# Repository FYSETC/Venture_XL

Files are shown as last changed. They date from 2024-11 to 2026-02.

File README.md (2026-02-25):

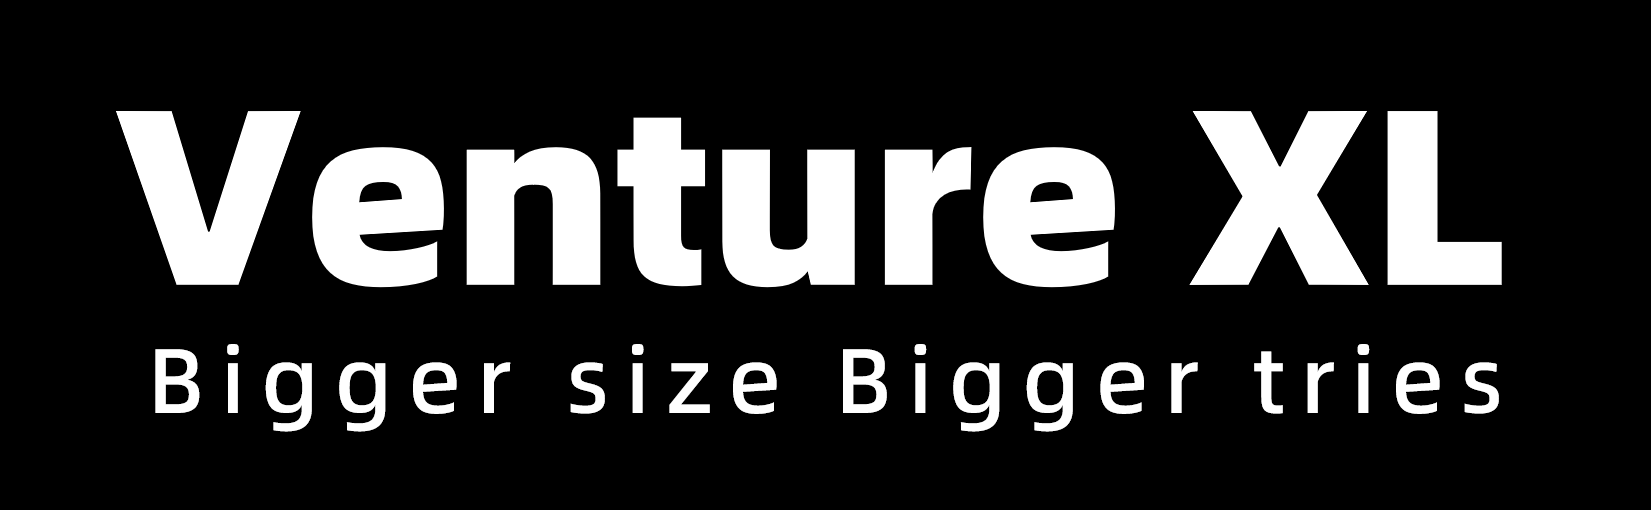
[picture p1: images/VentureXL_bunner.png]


# Introduction

The Venture XL, a 600mm3 coreXY printer kit, is inspired by the classic VORON V2.4. The key components of this kit are high-precision CNC-machined parts, demonstrating outstanding quality. Meanwhile, it comes with the necessary printing components and tools considerately, and the print head and control box have been pre - assembled, enabling you to start the installation process effortlessly without the need to prepare additional parts. Once the installation is completed, you can immediately engage in the printing work and enjoy an efficient and convenient printing experience.

It is equipped with a 550Mhz H723 single - chip microcomputer, an RK3568 with 4 cores at 2.0GHz, 2GB + 32GB for the host computer, a TMC5160 high - performance stepper motor driver, and a 7 - inch high - definition capacitive touch screen. With a printing speed of up to 500m/s and an acceleration of 50000, it not only brings an extremely fast printing experience but also creates a comfortable operation feeling for you.

The size of the machine frame is designed with reserved installation spaces for IDEX and AWD, providing you with broad possibilities for upgrade and modification, which is highly playable. Whether you are pursuing higher performance or personalized customization, you can find satisfaction here.

In addition, the complete enclosure design provides an insulated space for the printer, effectively maintaining the stability of the printing environment. At the same time, it also has powerful air - purification capabilities. It can support the printing of various consumables and, more importantly, minimize the potential threat of plastic particles to your health to the greatest extent, creating a safe and comfortable printing environment for you.

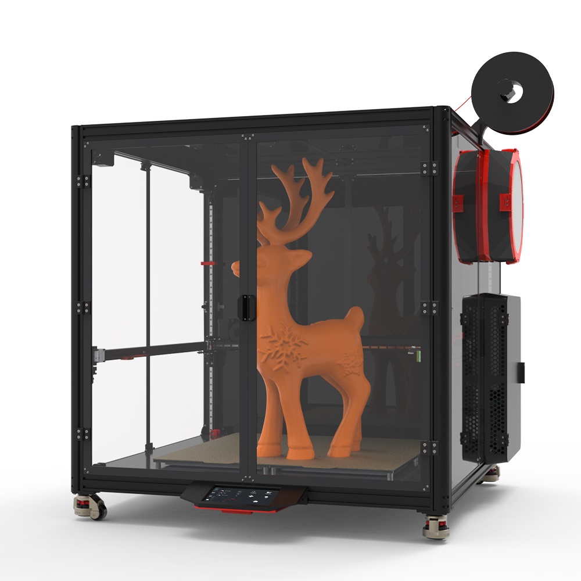
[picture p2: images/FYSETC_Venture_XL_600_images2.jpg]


# Features

## Electronics：

- RK3568 (2+32GB) 4 core A55 2.0GHz Host
- Spider Pro 2.0 Controller, 550Hz H723
- SB Combo V2 control board (Via CANBUS)
- 7-inch FHD optically bonded capacitive touch screen
- RGB lighting system , Horizontal RGB lighting (84 LEDs) & SB LOGO RGB (10 LEDs) & Vertical RGB lighting (2x84 LEDs)
- Dual 350W PSU, 48V+24V
- BIG5160+TMC2209 stepper motor driver
- High-power 63A/40A contactor
- Four-zone independent control hot bed
- Pre-assembled independent control box
- 4xZ reduction motor
- 2.5A high temperature, high torque XY motor
- Cartographer 3D Eddy Current Sensor
- Filament sensor
- Logitech C270 Camera 

## Mechanical

- Super large size: 910x910x940mm, can meet AWD or IDEX upgrade modification;

- Enclosed cavity, more materials can be printed, healthier printing method, the box is sealed by segmented assembly, easy to install and ensure structural strength;

- Compatible with Nevermore StealthMax air filter, the air quality in the box is guaranteed to be pollution-free when the box is sealed;

- 4040 aluminum profile frame, light and high strength;

- CNC precision-machined independent four-zone printing platform, can be fine-tuned according to flatness;

- Drag chain system;

- 12mm linear guide, 9mm super wear-resistant belt;

- Aluminum alloy external electric control box that can be placed arbitrarily (left/right/back), connect the line;

- CNC aluminum alloy link components to ensure the structural strength of the equipment;

- Z-axis 27:1 reduction motor ensures that the Z-axis is more stable and does not slip when the machine is running or stopped;

- IDMCNC metal bracket can withstand high temperature challenges and ensure stability. In a high-temperature printing environment, it will not deform or fail, ensuring long-lasting and reliable performance. The bracket weighs only 26g, which is lighter than TAP leveling and old-style proximity switches. The bracket weighs only 26g, which is lighter than TAP leveling and old-style proximity switches, reducing inertia and improving speed, accuracy and printing quality;

- Can hang 5KG large rolls of consumables, and there is no need to frequently replace consumables during printing;

- 40KG load Foma wheel allows the equipment to be stationed and transported at any time

# Bill of Materials

| Index | Sort | Component | Qty |
| ----- | --- | --- | --- |
| 1 | Fasteners | Venture XL Fasteners Pack | 1 SET  |
| 2 | Motion | GATES GT2 Open Belt LL-2GT-9 (9mm wide) - 3400mm | 2 PCS  |
| 3 | Motion | GATES GT2 Open Belt LL-2GT-9 (9mm wide) - 1800mm | 4 PCS  |
| 4 | Motion | GT2 20T Toothed Idler (8mm ID 9mm W) | 4 PCS  |
| 5 | Motion | GT2 20T Toothed Idler (5mm ID 9mm W) | 2 PCS  |
| 6 | Motion | F695-2RS Bearing | 48 PCS |
| 7 | Motion | 695-ZZ Bearing | 24 PCS |
| 8 | Motion | 5x29mm Shaft | 4 PCS  |
| 9 | Motion | MGN9H Linear Rail and Carriage 720mm | 4 PCS  |
| 10 | Motion | MGN9H Linear Rail and Carriage 760mm | 2 PCS  |
| 11 | Motion | MGN12H Linear Rail and Carriage 760mm | 1 PCS  |
| 12 | Vibration Management | Universal Fomar Caster | 4 PCS  |
| 13 | Electronics | Stealthburner CAN Toolhead Board | 1 SET  |
| 14 | Electronics | X AXIS ENDSTOP OMRON MICROSWITCH | 1 SET  |
| 15 | Electronics | Y AXIS ENDSTOP OMRON MICROSWITCH | 1 SET  |
| 16 | Electronics | Cartographer 3D Eddy Current Sensor | 1 SET  |
| 17 | Electronics | NeoPixel RGBW Mini Button PCB LED | 1 SET  |
| 18 | Electronics | Four-way solid state relay | 1 PCS  |
| 19 | Electronics | AC contactor | 1 PCS  |
| 20 | Electronics | Rocker Switch | 1 PCS  |
| 21 | Electronics | AC pin socket | 1 PCS  |
| 22 | Electronics | 42HSC8418-19PG27S(check [here](https://github.com/FYSETC/FYSETC-MOTORS/tree/main/42HSC8418-19PG27S)) | 4 PCS  |
| 23 | Electronics | 42HSC8418-37(check [here](https://github.com/FYSETC/FYSETC-MOTORS/tree/main/42HSC8418-37))  | 2 PCS  |
| 24 | Electronics | 40x40x10 Axial Fan (24V)  Dual Ball Bearing with heat sink | 2 PCS  |
| 25 | Electronics | G36HSY4405-6D-60(check [here](https://github.com/FYSETC/FYSETC-VORON-2.4-R2-Pro/tree/main/Docs/Stepper%20motor%20parameters)) | 1 PCS  |
| 26 | Electronics | Meanwell 350W-24V Power supply | 1 PCS  |
| 27 | Electronics | Meanwell350W-48V Power supply | 1 PCS  |
| 28 | Electronics | 30x30x7 Axial Fan (24V) | 1 PCS  |
| 29 | Electronics | 40x40x10 Axial Fan (24V)  Dual Ball Bearing | 1 PCS  |
| 30 | Electronics | 50x50x15 Centrifugal Fan (24V)  Dual Ball Bearing | 1 PCS  |
| 31 | Electronics | 90x90x15 Axial Fan (24V)  Dual Ball Bearing | 1 PCS  |
| 32 | Electronics | Keystone CAT6 Insert | 1 PCS  |
| 33 | Electronics | Terminal block (one in, four out) | 1 PCS  |
| 34 | Electronics | C13 Power Cord / NEMA5-20-C19 | 1 PCS  |
| 35 | Electronics | Gantry light bar power board | 1 PCS  |
| 36 | Electronics | Gantry light bar | 1 PCS  |
| 37 | Electronics | Lighting strips | 1 PCS  |
| 38 | Electronics | C270 Camera | 1 PCS  |
| 39 | Electronics | Electronic box (assembled ) | 1 PCS  |
| 40 | Controller | ~~sdcard 16GB~~ | 1 PCS  |
| 41 | Controller | USB2.0 A-C cable &  USB3.0 A-A cable | 1 PCS  |
| 42 | Controller | Spider_Pro_V1.0 | 1 PCS  |
| 43 | Controller | TMC2209 Stepper Motor Driver | 4 PCS  |
| 44 | Controller | BIG 5160 Stepper Motor Driver | 2 PCS  |
| 45 | Controller | 7-inch screen controller assembly set | 1 SET  |
| 46 | Frame | OpenBuilds | 12 PCS |
| 47 | Frame | Misumi sectional profile Kit（23 Pcs） | 1 SET  |
| 48 | Frame | Sealing profile kit（12 Pcs） | 1 SET  |
| 49 | Misc | PTFE Tube (4mm OD 2mm ID) - 3m | 1 PCS  |
| 50 | Misc | 6x3mm Neodimium Magnet | 12 PCS |
| 51 | Misc | Stealthburner kits | 1 SET  |
| 52 | Misc | PH2.0 2/3/4 Pin Plastic shell | 1 SET  |
| 53 | Misc | XH2.54 2/3/4 Pin Plastic shell | 1 SET  |
| 54 | Mics | Zip ties | 1 SET  |
| 55 | Mics | Saddle type cable tie holder | 1 SET  |
| 56 | Cables | Cable Kit（Pre-crimped terminals and longer wire lengths with label） | 1 SET  |
| 57 | Cables | VORON Chain Kit (10X10mm) | 3 PCS  |
| 58 | Panels | Bottom / Back / Side / Front / Top / Electric box Panels | 13 PCS |
| 59 | Buildplate | 6061 Plate - 302X302x5mm （Surface milling improve flatness） | 4 PCS  |
| 60 | Buildplate | Silicone AC Heater - 250x250mm (450W)+Thermal Fuse RH15A125（Pluggable） | 4 PCS  |
| 61 | Buildplate | JanusBPS Textured steel plate 605 x 605mm （Double-sided powder gold） | 1 PCS  |
| 62 | Buildplate | Scratch-proof Magnetic stickers 300X300mm thickness 1.5mm | 1 PCS  |
| 63 | Buildplate | Hotbed Insulation cotton thickness 5mm | 1 PCS  |
| 64 | Buildplate | VORON hot bed PEI limit baffle | 1 PCS  |
| 65 | Buildplate | VORON Hotbed nylon column | 1 SET  |
| 66 | Buildplate | Hot bed leveling spring | 1 SET  |
| 67 | Buildplate | VORON IDM Scanner CNC 9mm belt | 1 SET  |
| 68 | Tool | Electric soldering iron（With 500mm tin wire） | 1 PCS  |
| 69 | Tool | Heat-inserted nut kit | 1 SET  |
| 70 | Tool | Cutting pliers | 1 PCS  |
| 71 | Tool | Tweezers | 1 PCS  |
| 72 | Tool | Screwdriver (Phillips/Slotted) | 1 SET  |
| 73 | Tool | Hexagonal wrenchs | 1 SET  |
| 74 | Tool | Thermal silica | 1 PCS  |
| 75 | Tool | Key Puller | 1 PCS  |
| 76 | Misc | 3M VHB Tape 5952 | 1 PCS  |
| 77 | Tool | Shielding tape | 1 PCS  |
| 78 | Tool | Acetate cloth tape | 1 PCS  |
| 79 | Tool | Steel brush | 1 PCS  |
| 80 | Mics | Nevermore StealthMax | 1 SET  |
| 81 | Mics | Hinge | 8 PCS  |
| 82 | Mics | Braided Sleeve | 1 SET  |
| 83 | Mics | Aluminum profile flat sealing strip | 1 SET  |
| 84 | Mics | The standby line 3m | 1 PCS  |

# To Do Task

As an open source machine, it has unlimited possibilities. We will do our best to improve its information and tutorials. At the same time, we also invite professional players to contribute their ideas and strength. Below is part of our task progress, welcome to claim it.

|  TASK  | STATUS |  Author |
| ---- | ---- | ---- |
| Instruction manual: Paper wiring diagram included with the kit | [x] | FYSETC |
| Instruction manual: Quick guide to simple configuration included with the kit | [x] | FYSETC |
| Tutorial: Wiring tutorial | (i) | FYSETC |
| Tutorial: Structural installation video | [i] | FYSETC |
| Tutorial: Configuration tutorial | [x] | FYSETC |
| Tutorial: Common problems and solutions | (i) | FYSETC |
| Tutorial: Common slicing software configuration, Prusa Slicer / Bambu Slicer / Orca Slicer | [x] | FYSETC |
| Tutorial: Combo V2 USB usage guide | |  |
| Tutorial: AWD modification guide | | |
| Tutorial: IDEX modification tutorial | | |
| Tutorial: A more perfect wiring tutorial | (i) | Esoterical |
| Tutorial: Structural installation video | | |
| Tutorial: Wiring tutorial | | |
| Tutorial: Configuration tutorial | | |
| Evaluation: Speed limit | | |
| Evaluation: Common problems and solutions | | |

# Known issue

1.  Instructions for use of motor connection wire:
    Z0 and Z3 motors need to use 3.5m connecting wires, Z1 motor uses 1.85m connecting wires, and the connecting wires of Z2 motor and B motor are swapped to solve the problem of short connecting wire of B motor. A Motor connection line remains unchanged
    
2. Update Notes

| Column |images |Installation location |Download Link | |
| - | - | - | - | - |
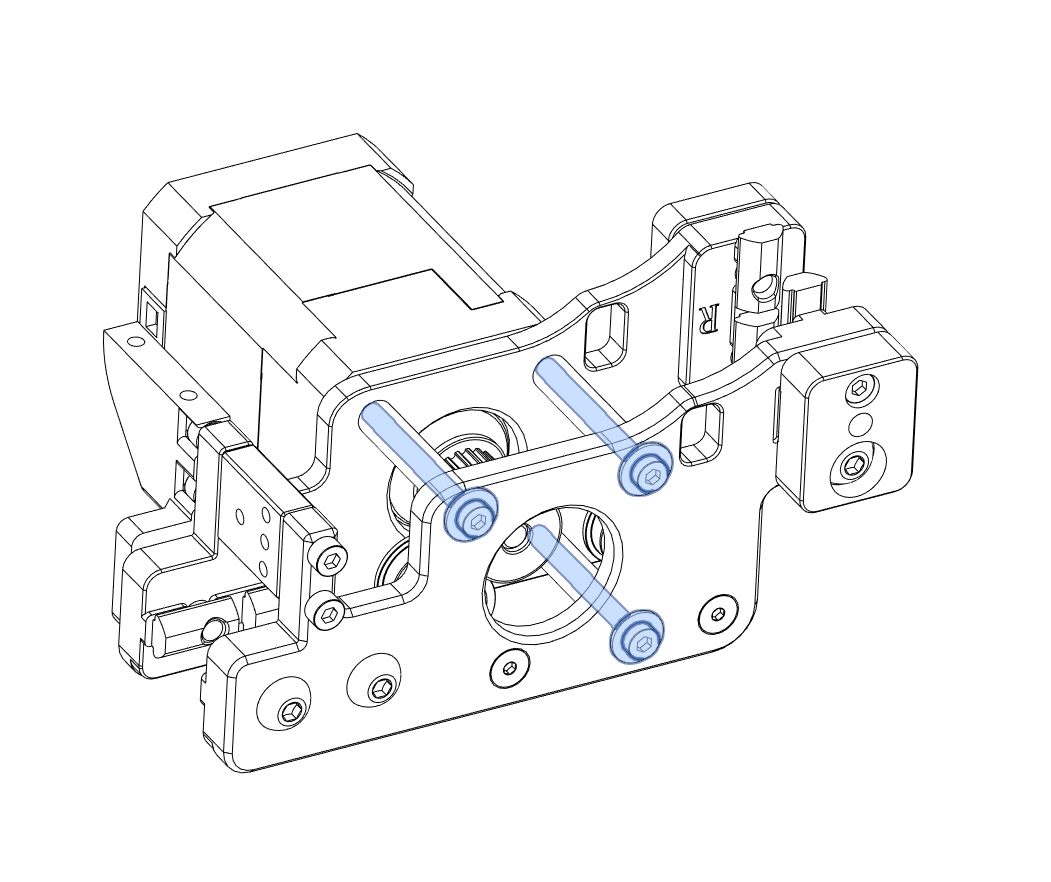
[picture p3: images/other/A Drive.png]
A Drive.png
|1 | |Manual page 26 | |The M3x40 motor mounting screws are a bit long, so you can use M3x38 instead, or add M3 washers and use M3x40 for installation. |
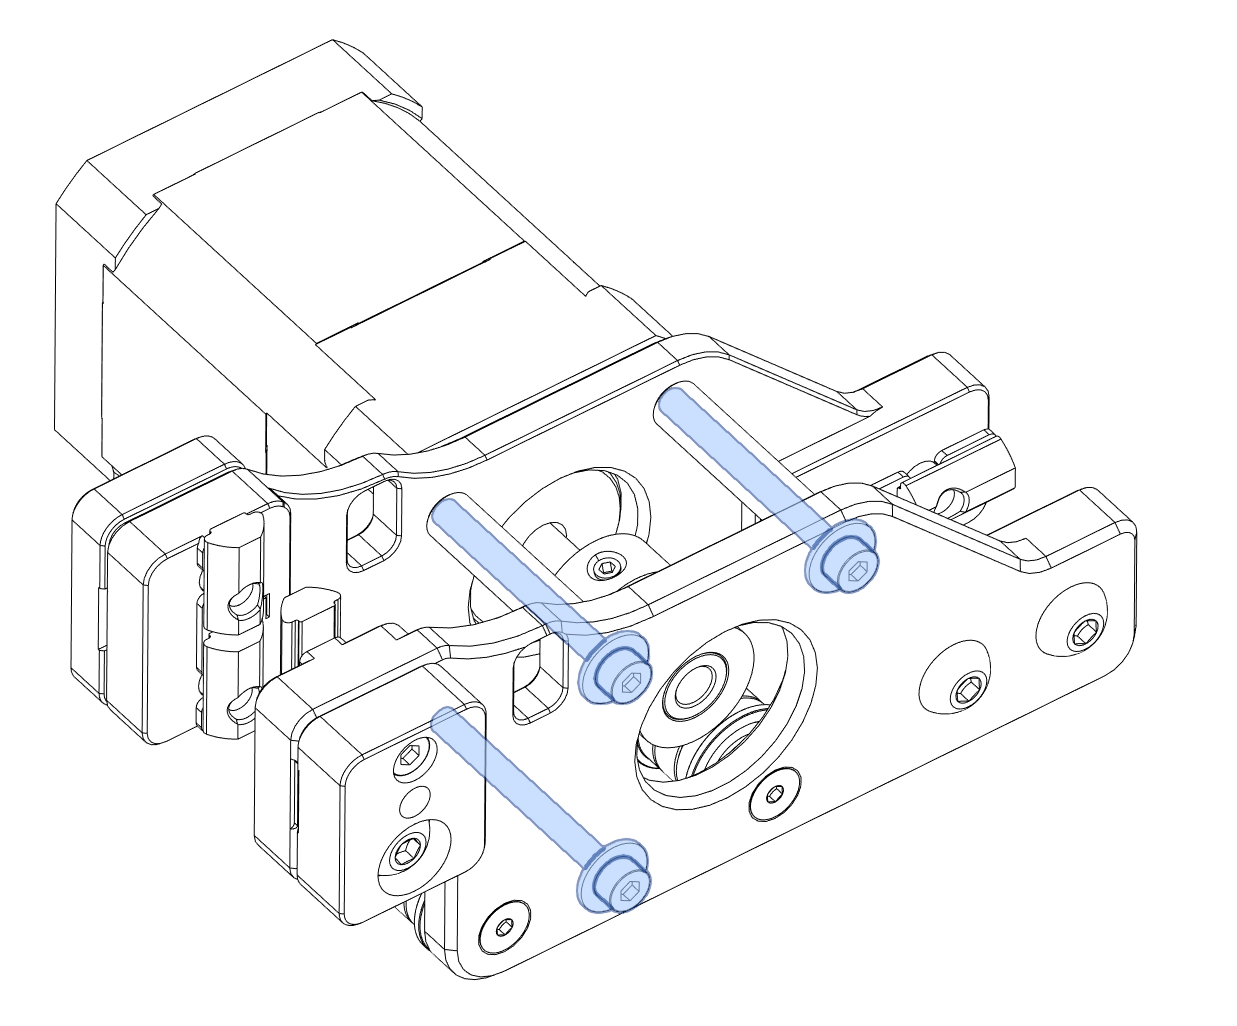
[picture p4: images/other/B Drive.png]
B Drive.png
|2 | |Manual page 27 | |The M3x40 motor mounting screws are a bit long, so you can use M3x38 instead, or add M3 washers and use M3x40 for installation.  |
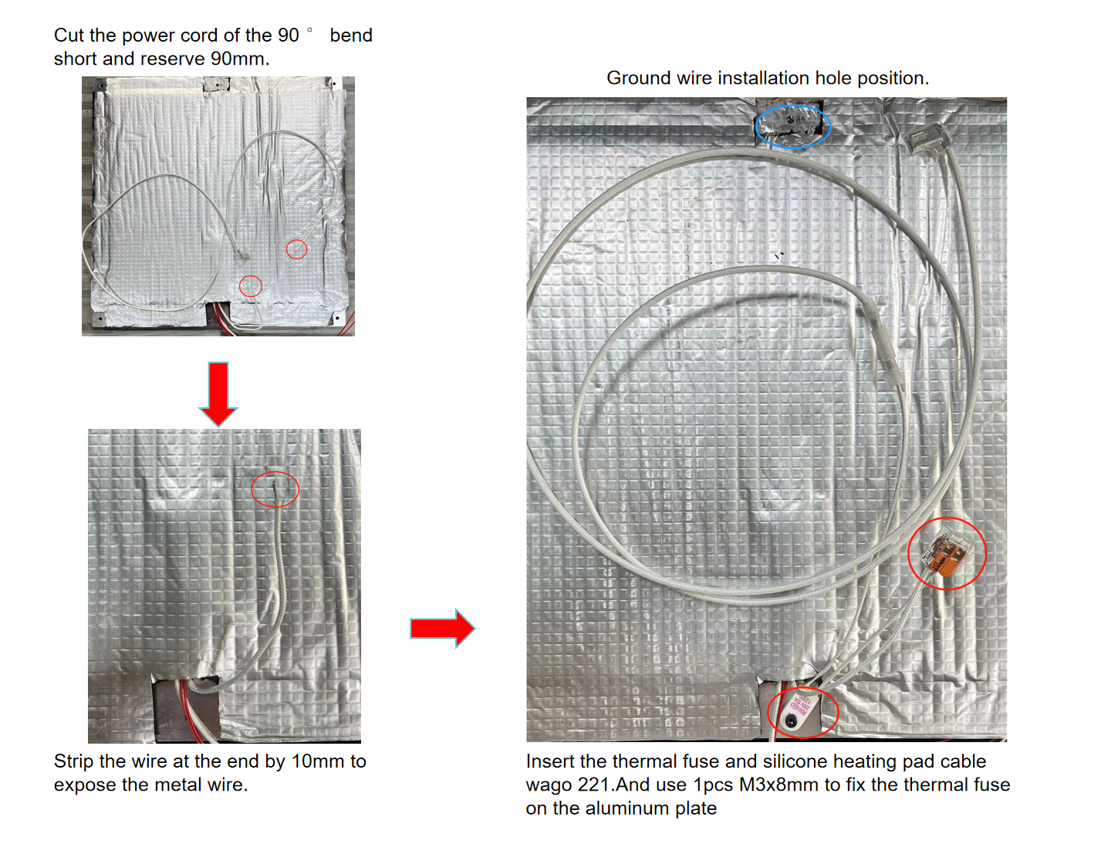
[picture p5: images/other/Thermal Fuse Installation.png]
Thermal Fuse Installation.png
|3 | |Manual page 43 | |Added 4 pcs hot bed thermal fuse |
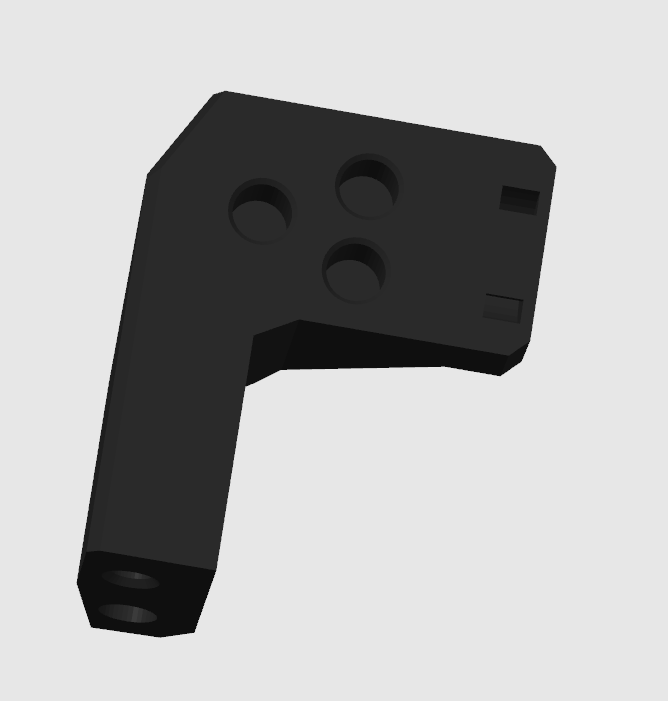
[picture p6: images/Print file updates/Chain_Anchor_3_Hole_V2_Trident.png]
|4 | |Manual page 48 |[here](https://github.com/FYSETC/Venture_XL/blob/main/STLs/Need%20to%20print%20the%20document%20yourself/Stealthburner/Chain_Anchor_3_Hole_V2_Trident.STL) | |
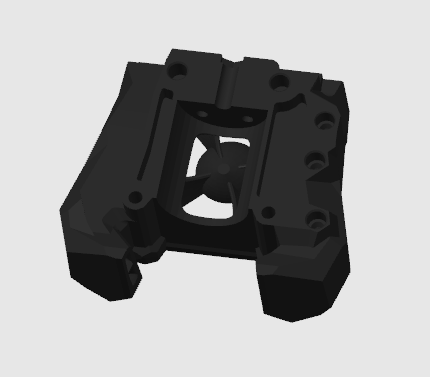
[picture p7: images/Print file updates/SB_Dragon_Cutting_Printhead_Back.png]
|5 | |Manual page 48 |[here](https://github.com/FYSETC/Venture_XL/blob/main/STLs/Need%20to%20print%20the%20document%20yourself/Stealthburner/SB_Dragon_Cutting_Printhead_Back.STL) | |
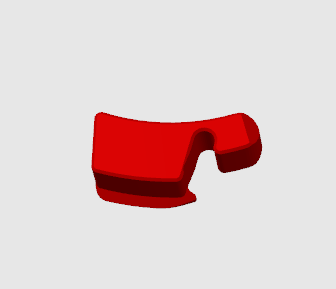
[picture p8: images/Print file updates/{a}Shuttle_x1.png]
|6 | |Manual page 49 |[here](https://github.com/FYSETC/Venture_XL/blob/main/STLs/Need%20to%20print%20the%20document%20yourself/Stealthburner/%7Ba%7DShuttle_x1.STL) | |
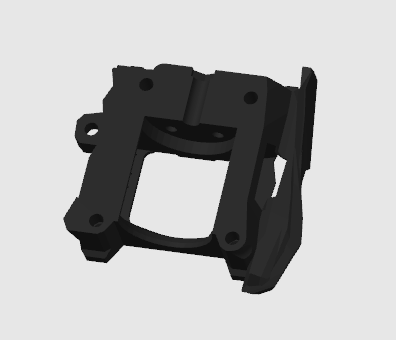
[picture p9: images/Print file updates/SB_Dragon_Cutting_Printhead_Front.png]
|7 | |Manual page 50 |[here](https://github.com/FYSETC/Venture_XL/blob/main/STLs/Need%20to%20print%20the%20document%20yourself/Stealthburner/SB_Dragon_Cutting_Printhead_Front.STL) | |
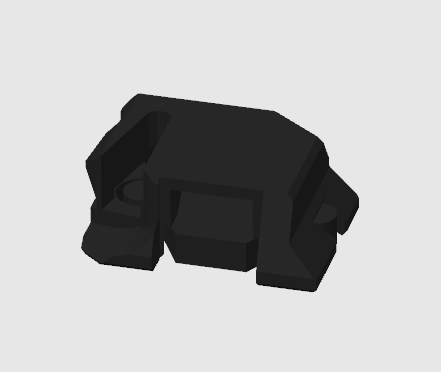
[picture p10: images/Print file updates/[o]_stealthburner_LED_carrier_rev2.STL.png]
|8 | |Manual page 52 |[here](https://github.com/FYSETC/Venture_XL/blob/main/STLs/Need%20to%20print%20the%20document%20yourself/Stealthburner/%5Bo%5D_stealthburner_LED_carrier_rev2.STL.stl) | |
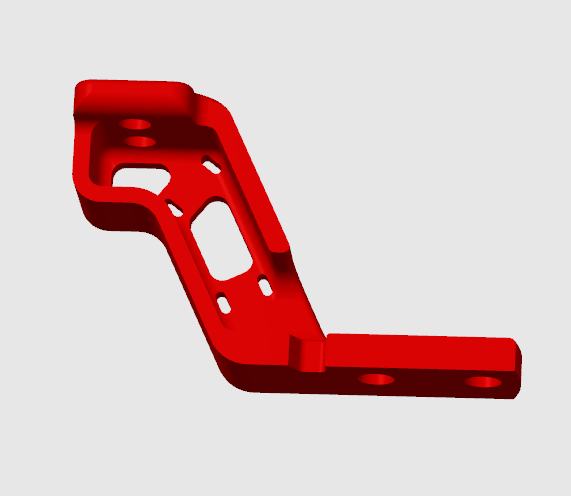
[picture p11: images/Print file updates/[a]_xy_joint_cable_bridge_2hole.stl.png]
|9 | |Manual page 53 |[here](https://github.com/FYSETC/Venture_XL/blob/main/STLs/Need%20to%20print%20the%20document%20yourself/XY_Joints/%5Ba%5D_xy_joint_cable_bridge_2hole.stl.stl) | |
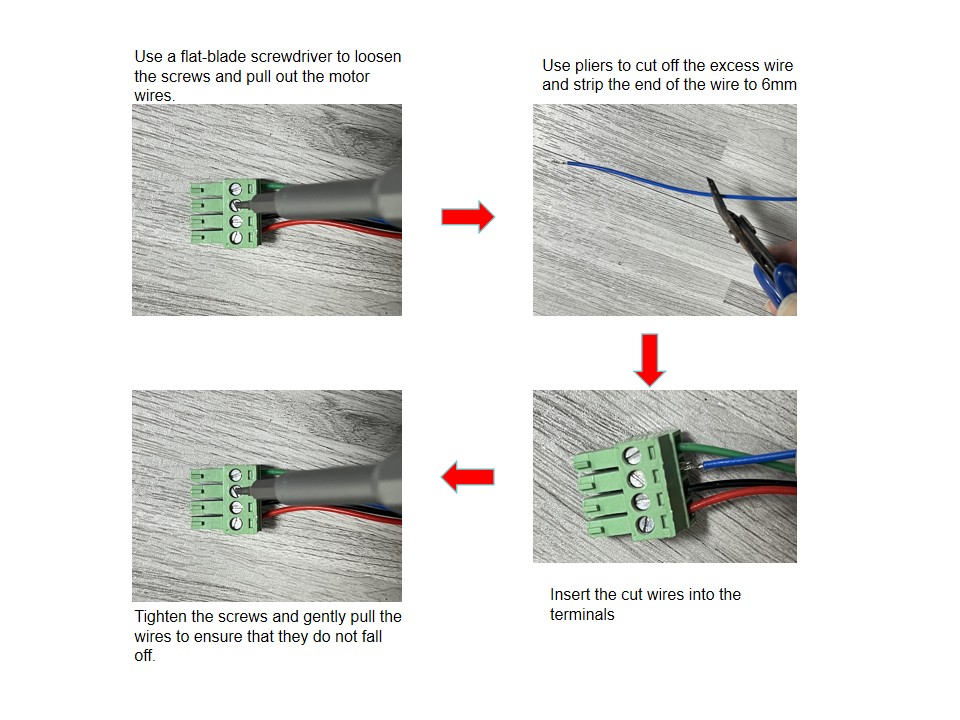
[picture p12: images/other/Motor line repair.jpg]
Motor line repair.jpg
|10 | | | |Motor line repair |
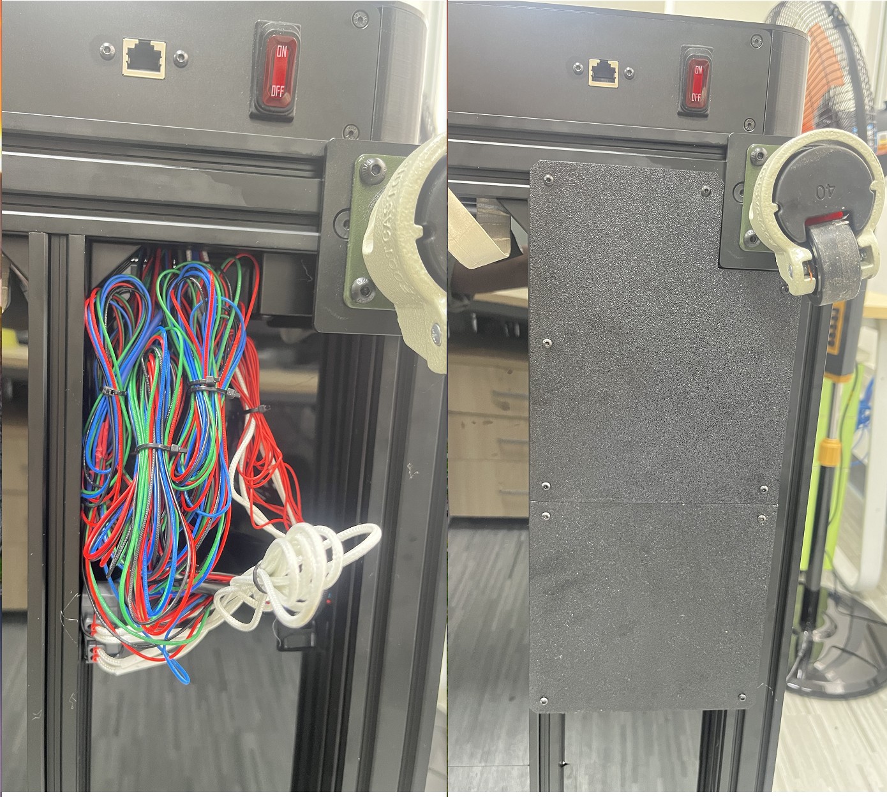
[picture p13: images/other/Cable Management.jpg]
Cable Management.jpg
|11 | |Manual page 59 |[here](https://github.com/FYSETC/Venture_XL/blob/main/STLs/Need%20to%20print%20the%20document%20yourself/Under%20Floor%20Wire%20Cover/Under%20Floor%20Wire%20Cover_1_x1.STL)  [here](https://github.com/FYSETC/Venture_XL/blob/main/STLs/Need%20to%20print%20the%20document%20yourself/Under%20Floor%20Wire%20Cover/Under%20Floor%20Wire%20Cover_2_x1.STL) |Add bottom cable cover |

**Please provide the order number to contact customer service to collect the supplementary accessory package.**

3. Notice

Venture_XL CAD need to use WinRAR to decompress, otherwise the file cannot be opened.

4.Instructions

We have updated the installation guide on WIKI,；
link:(https://wiki.fysetc.com/docs/Venture_XL)

5.Version 2 - Spider King

The motherboard has been updated and replaced with Spider King.
Replaced mainboard, updated wiring diagram

# Thanks to
Here I would like to express my gratitude and support to Esoterical、 RichardTHF and many others. Your suggestions have helped us a lot - you all have my most sincere thanks.

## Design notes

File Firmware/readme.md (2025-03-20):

RK3568 img: Mega 

https://mega.nz/fm/XEJgVJ6b

Cartographer:

https://docs.cartographer3d.com/cartographer-probe/installation-and-setup

Spider Pro:

https://github.com/FYSETC/Spider_Pro

SB Combo:

https://wiki.fysetc.com/SB_Combo_V2/

https://github.com/FYSETC/SB_Combo_V2

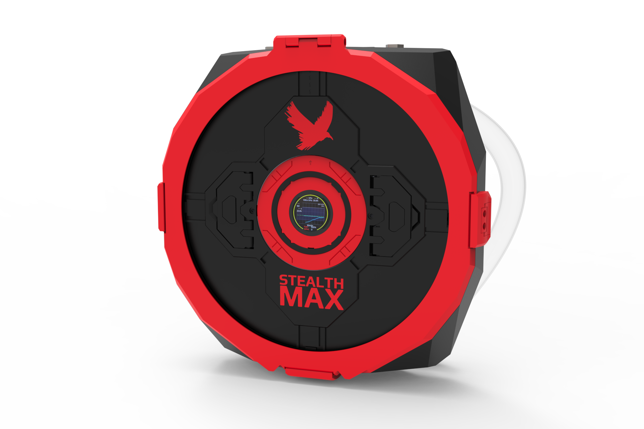
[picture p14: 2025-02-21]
images/Venture_XL_600_StealthMax.png

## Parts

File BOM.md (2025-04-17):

# Package list 

## Venture_XL V1.0

| Index | Sort | Component | Qty | Note |
| ----- | --- | --- | --- | --- |
| 1 | Fasteners | Venture XL Fasteners Pack | 1 SET  | |
| 2 | Motion | GATES GT2 Open Belt LL-2GT-9 (9mm wide) - 3400mm | 2 PCS  | |
| 3 | Motion | GATES GT2 Open Belt LL-2GT-9 (9mm wide) - 1800mm | 4 PCS  | |
| 4 | Motion | GT2 20T Toothed Idler (8mm ID 9mm W) | 4 PCS  | |
| 5 | Motion | GT2 20T Toothed Idler (5mm ID 9mm W) | 2 PCS  | |
| 6 | Motion | F695-2RS Bearing | 48 PCS | |
| 7 | Motion | 695-ZZ Bearing | 24 PCS | |
| 8 | Motion | 5x29mm Shaft | 4 PCS  | |
| 9 | Motion | MGN9H Linear Rail and Carriage 720mm | 4 PCS  | |
| 10 | Motion | MGN9H Linear Rail and Carriage 760mm | 2 PCS  | |
| 11 | Motion | MGN12H Linear Rail and Carriage 760mm | 1 PCS  | |
| 12 | Vibration Management | Universal Fomar Caster | 4 PCS  | |
| 13 | Electronics | Stealthburner CAN Toolhead Board | 1 SET  | |
| 14 | Electronics | X AXIS ENDSTOP OMRON MICROSWITCH | 1 SET  | |
| 15 | Electronics | Y AXIS ENDSTOP OMRON MICROSWITCH | 1 SET  | |
| 16 | Electronics | ADXL__Hybrid_IDM | 1 SET  | |
| 17 | Electronics | NeoPixel RGBW Mini Button PCB LED | 1 SET  | |
| 18 | Electronics | Four-way solid state relay | 1 PCS  | |
| 19 | Electronics | AC contactor | 1 PCS  | |
| 20 | Electronics | Rocker Switch | 1 PCS  | |
| 21 | Electronics | AC pin socket | 1 PCS  | |
| 22 | Electronics | 42HSC8418-19PG27S | 4 PCS  | |
| 23 | Electronics | 42HSC8418-37 | 2 PCS  | |
| 24 | Electronics | 40x40x10 Axial Fan (24V)  Dual Ball Bearing with heat sink | 2 PCS  | |
| 25 | Electronics | G36HSY4405-6D-60(check [here](https://github.com/FYSETC/FYSETC-VORON-2.4-R2-Pro/tree/main/Docs/Stepper%20motor%20parameters)) | 1 PCS  | |
| 26 | Electronics | 350W-24V Power supply | 1 PCS  | |
| 27 | Electronics | 350W-48V Power supply | 1 PCS  | |
| 28 | Electronics | 30x30x7 Axial Fan (24V) | 1 PCS  | |
| 29 | Electronics | 40x40x10 Axial Fan (24V)  Dual Ball Bearing | 1 PCS  | |
| 30 | Electronics | 50x50x15 Centrifugal Fan (24V)  Dual Ball Bearing | 1 PCS  | |
| 31 | Electronics | 90x90x15 Axial Fan (24V)  Dual Ball Bearing | 1 PCS  | |
| 32 | Electronics | Keystone CAT6 Insert | 1 PCS  | |
| 33 | Electronics | Terminal block (one in, four out) | 1 PCS  | |
| 34 | Electronics | C13 Power Cord / NEMA5-20-C19 | 1 PCS  | |
| 35 | Electronics | Gantry light bar power board | 1 PCS  | |
| 36 | Electronics | Gantry light bar | 1 PCS  | |
| 37 | Electronics | Lighting strips | 1 PCS  | |
| 38 | Electronics | Camera | 1 PCS  | |
| 39 | Electronics | Electric box | 1 PCS  | |
| 40 | Controller | sdcard 16GB | 1 PCS  | |
| 41 | Controller | USB C cable | 1 PCS  | |
| 42 | Controller | Spider_Pro_V1.0 | 1 PCS  | |
| 43 | Controller | TMC2209 Stepper Motor Driver | 4 PCS  | |
| 44 | Controller | BIG 5160 Stepper Motor Driver | 2 PCS  | |
| 45 | Controller | 7-inch screen controller assembly (7-inch display + CM68 control board + display cable + CM68 radiator + 4010 cooling fan + printed housing) | 1 SET  | |
| 46 | Frame | OpenBuilds | 12 PCS | |
| 47 | Frame | Misumi sectional profile Kit（23 Pcs） | 1 SET  | |
| 48 | Frame | Sealing profile kit（12 Pcs） | 1 SET  | |
| 49 | Misc | PTFE Tube (4mm OD 2mm ID) - 3m | 1 PCS  | |
| 50 | Misc | 6x3mm Neodimium Magnet | 12 PCS | |
| 51 | Misc | Stealthburner挤出头打印件套件 | 1 SET  | upgrade |
| 52 | Misc | PH2.0 2/3/4 Pin Plastic shell | 1 SET  | |
| 53 | Misc | XH2.54 2/3/4 Pin Plastic shell | 1 SET  | |
| 54 | Mics | Zip ties | 1 SET  | |
| 55 | Mics | Saddle type cable tie holder | 1 SET  | |
| 56 | Cables | Cable Kit（Pre-crimped terminals and longer wire lengths with label） | 1 SET  | |
| 57 | Cables | VORON Chain Kit (10X10mm) | 3 PCS  | |
| 58 | Panels | Bottom / Back / Side / Front / Top / Electric box Panels | 13 PCS | |
| 59 | Buildplate | 6061 Plate - 302X302x5mm （Surface milling improve flatness） | 4 PCS  | |
| 60 | Buildplate | Silicone AC Heater - 250x250mm (450W) | 4 PCS  | |
| 61 | Buildplate | JanusBPS Textured steel plate 605 x 605mm （Double-sided powder gold） | 1 PCS  | |
| 62 | Buildplate | Scratch-proof Magnetic stickers 300X300mm thickness 1.5mm | 1 PCS  | |
| 63 | Buildplate | Hotbed Insulation cotton thickness 5mm | 1 PCS  | |
| 64 | Buildplate | VORON hot bed PEI limit baffle | 1 PCS  | |
| 65 | Buildplate | VORON Hotbed nylon column | 1 SET  | |
| 66 | Buildplate | Hot bed leveling spring | 1 SET  | |
| 67 | Buildplate | VORON IDM Scanner CNC 9mm belt | 1 SET  | |
| 68 | Tool | Electric soldering iron（With 500mm tin wire） | 1 PCS  | |
| 69 | Tool | Heat-inserted nut kit | 1 SET  | |
| 70 | Tool | Cutting pliers | 1 PCS  | |
| 71 | Tool | Tweezers | 1 PCS  | |
| 72 | Tool | Screwdriver (Phillips/Slotted) | 1 SET  | |
| 73 | Tool | Hexagonal wrenchs | 1 SET  | |
| 74 | Tool | Thermal silica | 1 PCS  | |
| 75 | Tool | Key Puller | 1 PCS  | |
| 76 | Misc | 3M VHB Tape 5952 | 1 PCS  | |
| 77 | Tool | Shielding tape | 1 PCS  | |
| 78 | Tool | Acetate cloth tape | 1 PCS  | |
| 79 | Tool | Steel brush | 1 PCS  | |
| 80 | Mics | Nevermore StealthMax | 1 SET  | |
| 81 | Mics | Hinge | 8 PCS  | |
| 82 | Mics | Braided Sleeve | 1 SET  | |
| 83 | Mics | Aluminum profile flat sealing strip | 1 SET  | |
| 84 | Mics | The standby line 3m | 1 PCS  | |

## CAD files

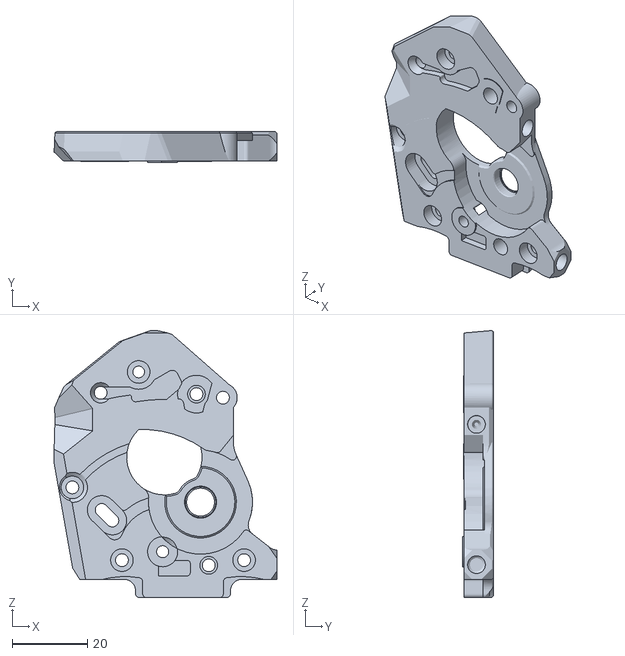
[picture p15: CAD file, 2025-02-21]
STLs/No printing required/Stealthburner/SB_CW1_Main_Body_Cutting_With_ECAS_x1.STL
59.1 x 8.20 x 70.8

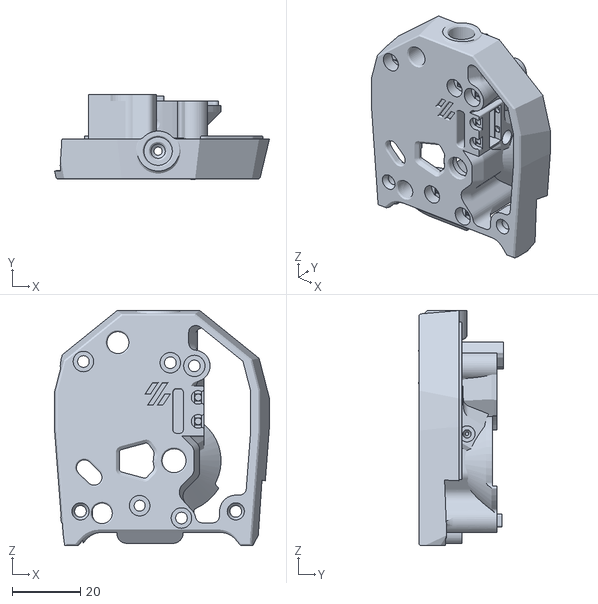
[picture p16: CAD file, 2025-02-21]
STLs/No printing required/Stealthburner/SB_CW2-1_Main_Body_Cutting_With_ECAS_x1.STL
62.8 x 24.7 x 68.7

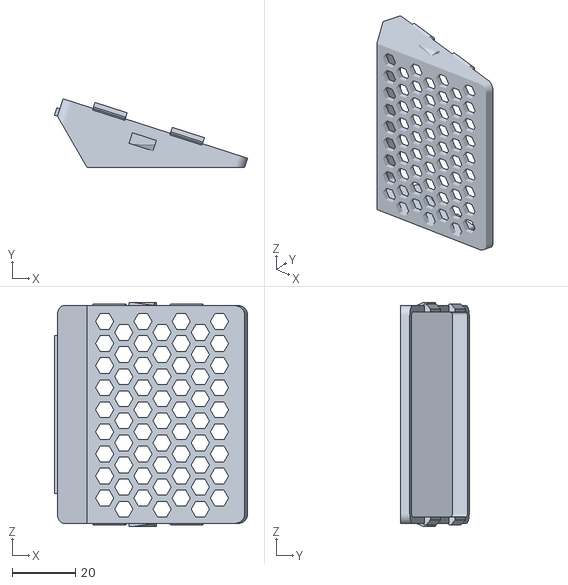
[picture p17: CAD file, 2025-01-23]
STLs/Already printed within the package/Display housing/7 inch display housing_3_x1.STL
61.2 x 21.7 x 71.0

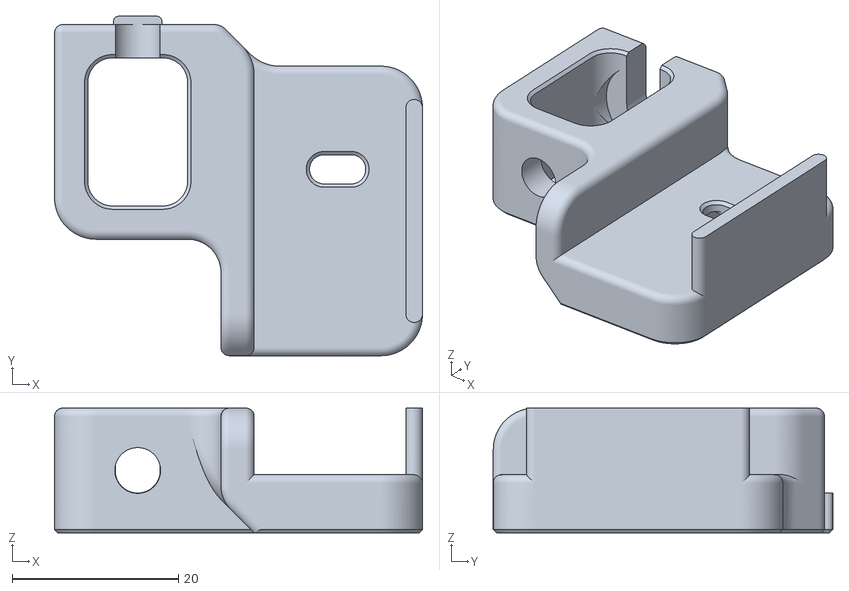
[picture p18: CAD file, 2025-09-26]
STLs/Already printed within the package/Drag chain fixing_2-black_X1.STL
44.2 x 40.8 x 15.0

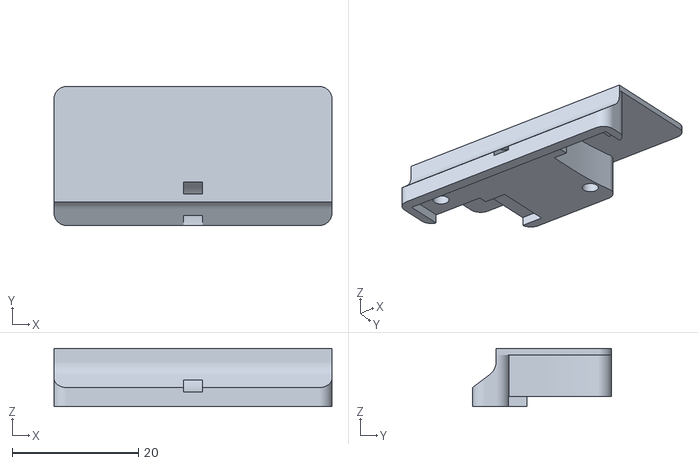
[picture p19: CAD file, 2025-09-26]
STLs/Already printed within the package/Gantry/Light bar power board_cover_black_x1.STL
44.0 x 22.0 x 9.20

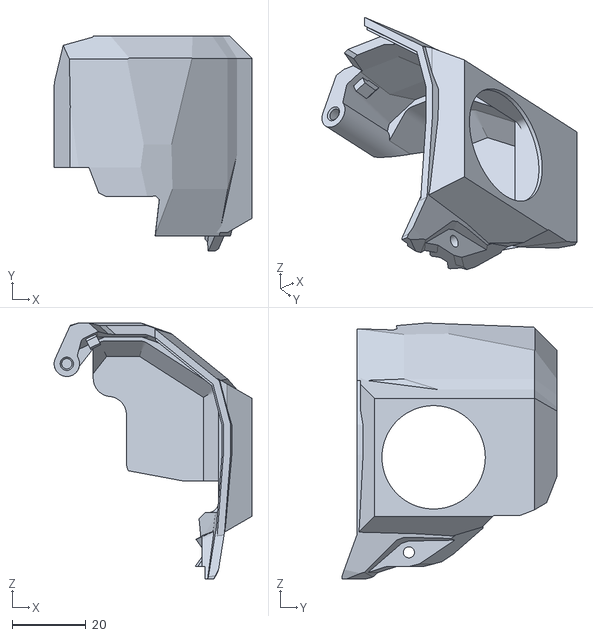
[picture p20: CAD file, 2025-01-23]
STLs/Already printed within the package/Gantry/X_Axis/Stealthburner/SB3010 Fan Cover.STL
53.6 x 58.2 x 69.4

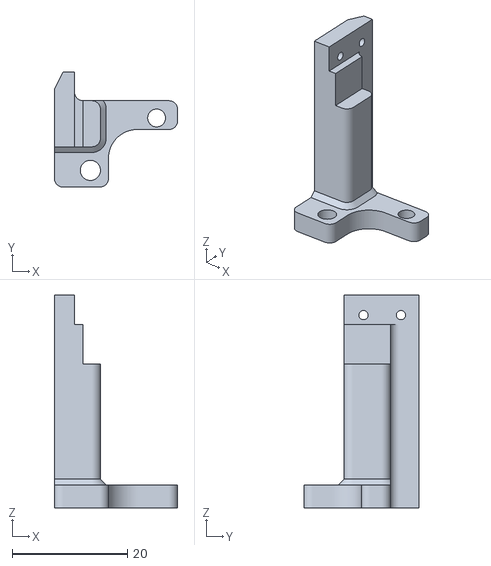
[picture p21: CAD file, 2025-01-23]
STLs/Already printed within the package/Gantry/Y limit bracket/Y limit bracket_x1.STL
21.4 x 20.0 x 37.0

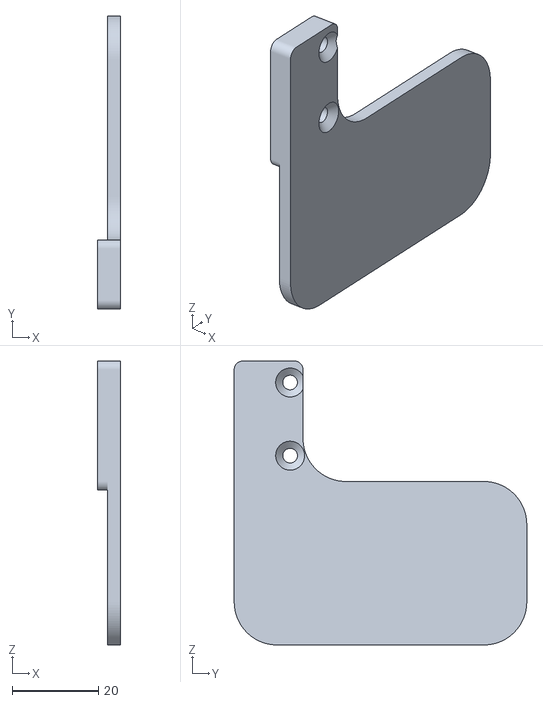
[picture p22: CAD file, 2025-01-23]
STLs/Already printed within the package/Gantry/Z axis drag chain limit/Z axis drag chain limit_1-2_x1.STL
5.30 x 68.0 x 66.0

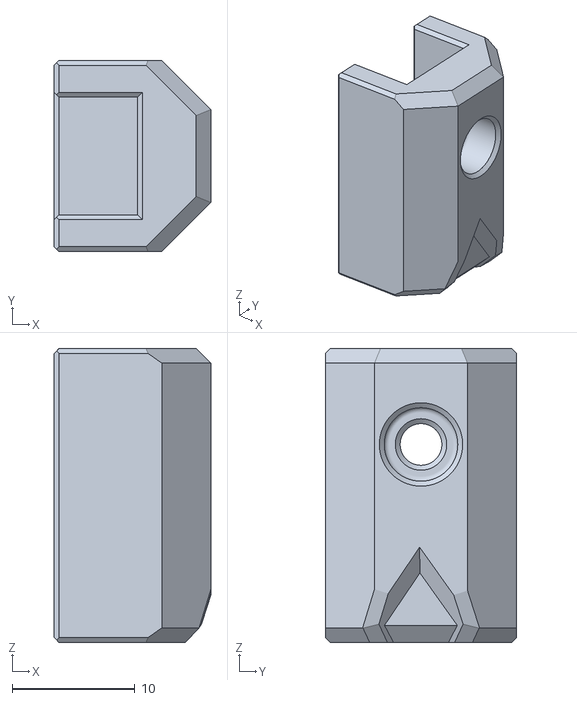
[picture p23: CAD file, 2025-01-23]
STLs/Already printed within the package/Gantry/Z-axis guide rail limit/Z-axis guide rail limit_x4.STL
12.8 x 15.6 x 24.0

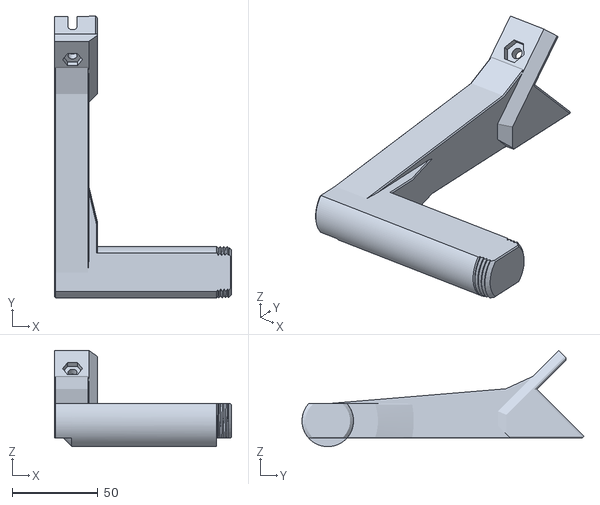
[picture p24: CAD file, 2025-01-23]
STLs/Already printed within the package/Material rack/Material rack_1_x1.STL
103.0 x 164.1 x 56.0

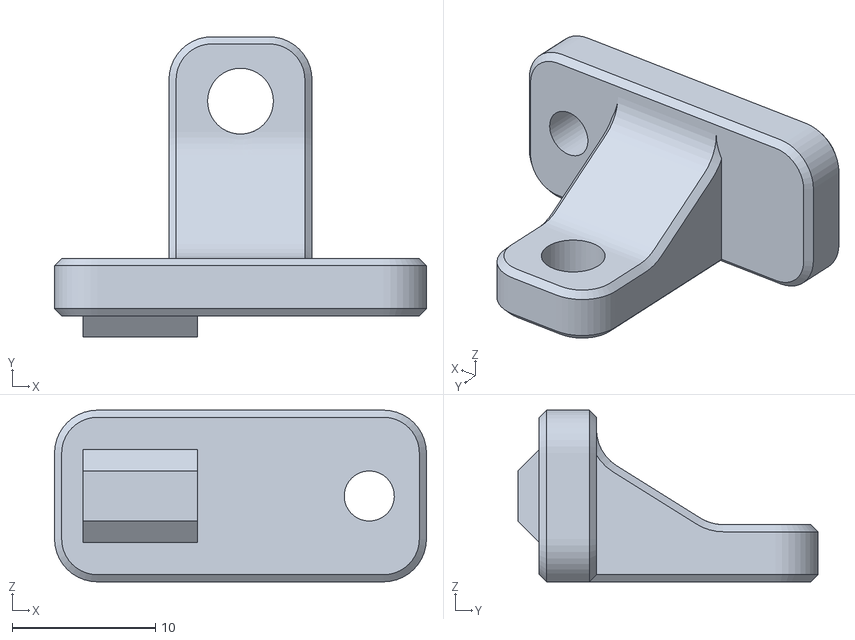
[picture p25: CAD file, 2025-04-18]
STLs/Need to print the document yourself/Acrylic plate fixing_black/Acrylic plate fixing_2_x10.STL
26.0 x 21.0 x 12.0

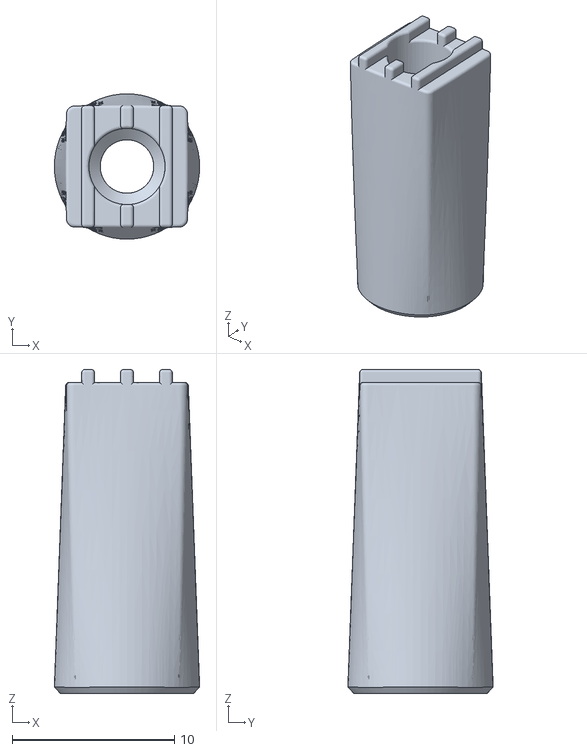
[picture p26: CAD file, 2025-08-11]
STLs/Need to print the document yourself/Depressor.stl
8.97 x 8.97 x 20.0

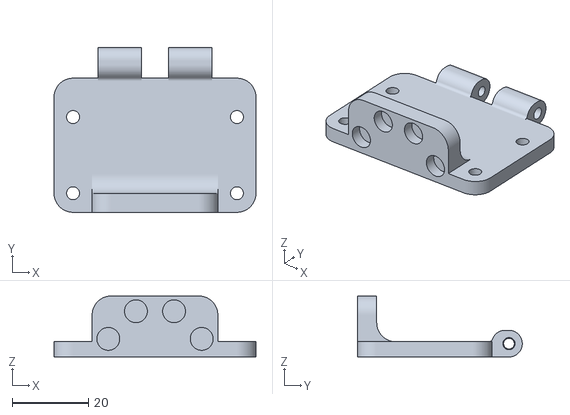
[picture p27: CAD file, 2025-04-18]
STLs/Need to print the document yourself/Door_black/Door Block + Camera Bracket_up_x1.STL
53.0 x 43.2 x 16.0

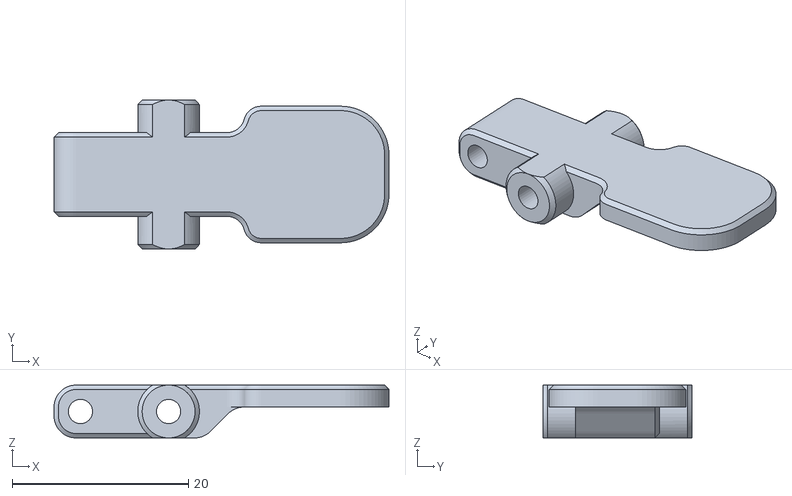
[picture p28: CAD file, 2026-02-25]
STLs/Need to print the document yourself/Electronics_Box/electronics_latch_pt3.stl
38.0 x 16.9 x 6.00

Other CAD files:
STLs/Need to print the document yourself/Nevermore StealthMax/1_FlowChamber/1.5_FanWirePin_Spare.stl
STLs/Need to print the document yourself/Nevermore StealthMax/2_MainChamber/2.9_CarbonBasketLidHandle_Spare.stl
STLs/Need to print the document yourself/Nevermore StealthMax/3-Lid/M_3.1_LidPanelHolder.stl
STLs/Need to print the document yourself/Nevermore StealthMax/4_AddOns/4.0.0_IntakeAdapterLeft.stl
STLs/Already printed within the package/Display housing/7 inch display housing_1_x1.STL
STLs/Already printed within the package/Display housing/7 inch display housing_2_x1.STL
STLs/Already printed within the package/Drag chain fixing_1-red_X1.STL
STLs/Already printed within the package/Drag chain fixing_3-black_X1.STL
STLs/Already printed within the package/Drag chain fixing_4-black_X1.STL
STLs/Already printed within the package/Drag chain fixing_5-black_X1.STL
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

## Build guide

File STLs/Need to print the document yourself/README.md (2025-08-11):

# Toolheads Knife Holder 

## Illustration



### Cutting point on gantry
- 1x M3x30/M3x35 BHCS
- 2x Threaded Insert M3*5.0xH4.0
- 2x M3 Nut
- 2x M3x8 FHCS
- 2x M3 T-Nut


<br>
<hr>

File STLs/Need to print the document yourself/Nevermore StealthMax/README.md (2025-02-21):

## Nevermore StealthMax Air Filter Description

### Nevermore StealthMax

This is a project from the Nevermore3d, Nevermore StealthMax. We made a little upgrade and improvement on the basis of this project, and provided a complete set of information. Thanks to the open source materials and support provided by the Nevermore3d, and hope you like it. You can find Nevermore3d official information below. 

1.StealthMax Official website： 

https://github.com/nevermore3d/StealthMax

Venture_XL_600_StealthMax

# Installation Guide

FYSETC Venture_XL_StealthMax Assembly manual [here]([FYSETC/Venture_XL](https://github.com/FYSETC/Venture_XL/tree/main) ).

# Firmware&OS

# FAQ

### Original Venture_XL_StealthMax FAQ [here]((https://github.com/nevermore3d/StealthMax/tree/main/STLs) ).

### FYSETC Venture_XL_StealthMax FAQ

# Support

FYSETC Facebook group:

<https://www.facebook.com/groups/238970713918171>

FYSETC Discord:

<https://discord.gg/T3XcJPgr>

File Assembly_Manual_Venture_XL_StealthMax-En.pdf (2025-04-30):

# Venture XL Nevermore StealthMax

☆ 3D printer air purification system promotes a safer and healthier printing environment.

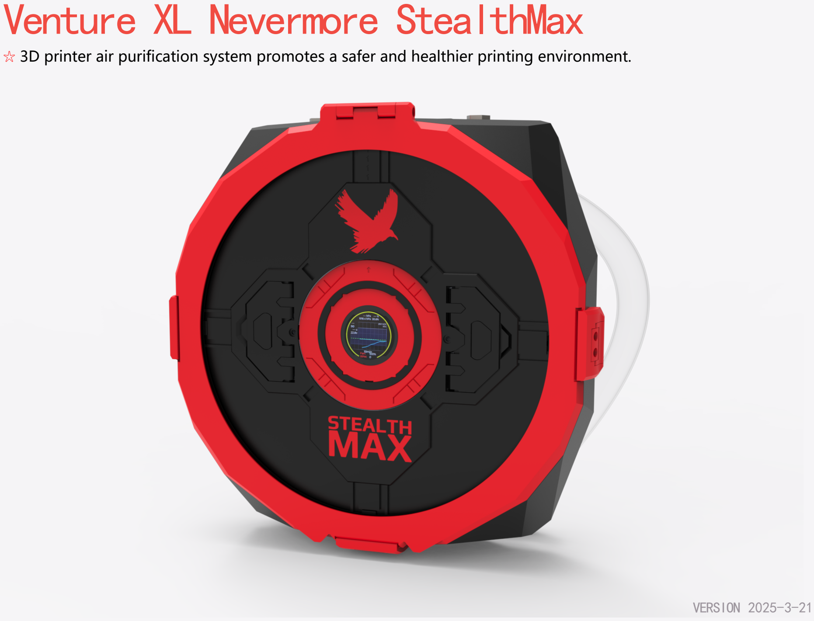
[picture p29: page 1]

VERSION 2025-3-21

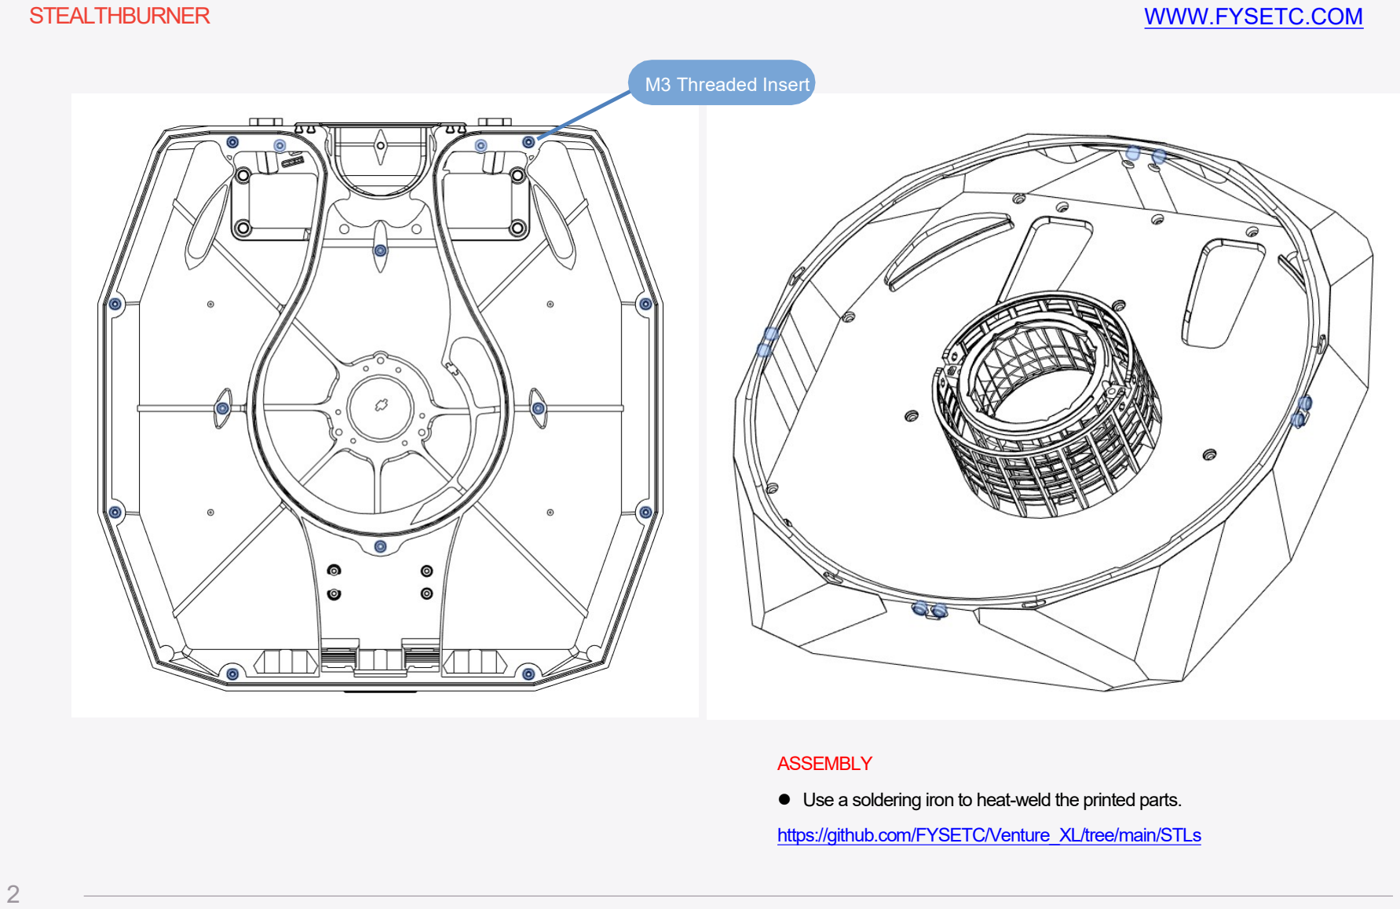
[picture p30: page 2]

### WWW.FYSETC.COM

ASSEMBLY
l Use a soldering iron to heat-weld the printed parts. https://github.com/FYSETC/Venture_XL/tree/main/STLs

### STEALTHBURNER

M3 Threaded Insert

2

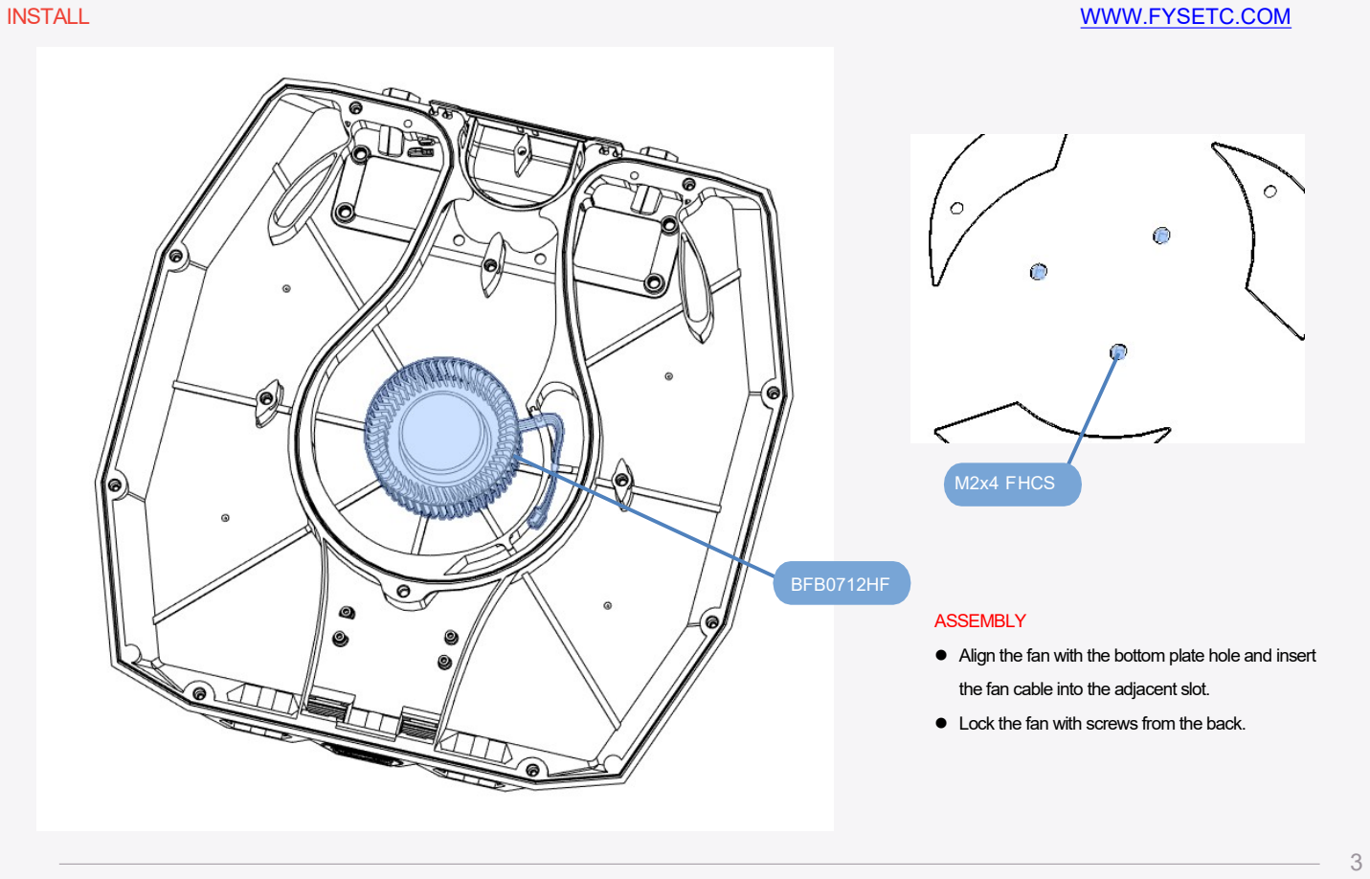
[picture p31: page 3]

### WWW.FYSETC.COM

3

### INSTALL

M2x4 FHCS

BFB0712HF

ASSEMBLY
l Align the fan with the bottom plate hole and insert the fan cable into the adjacent slot.
l Lock the fan with screws from the back.

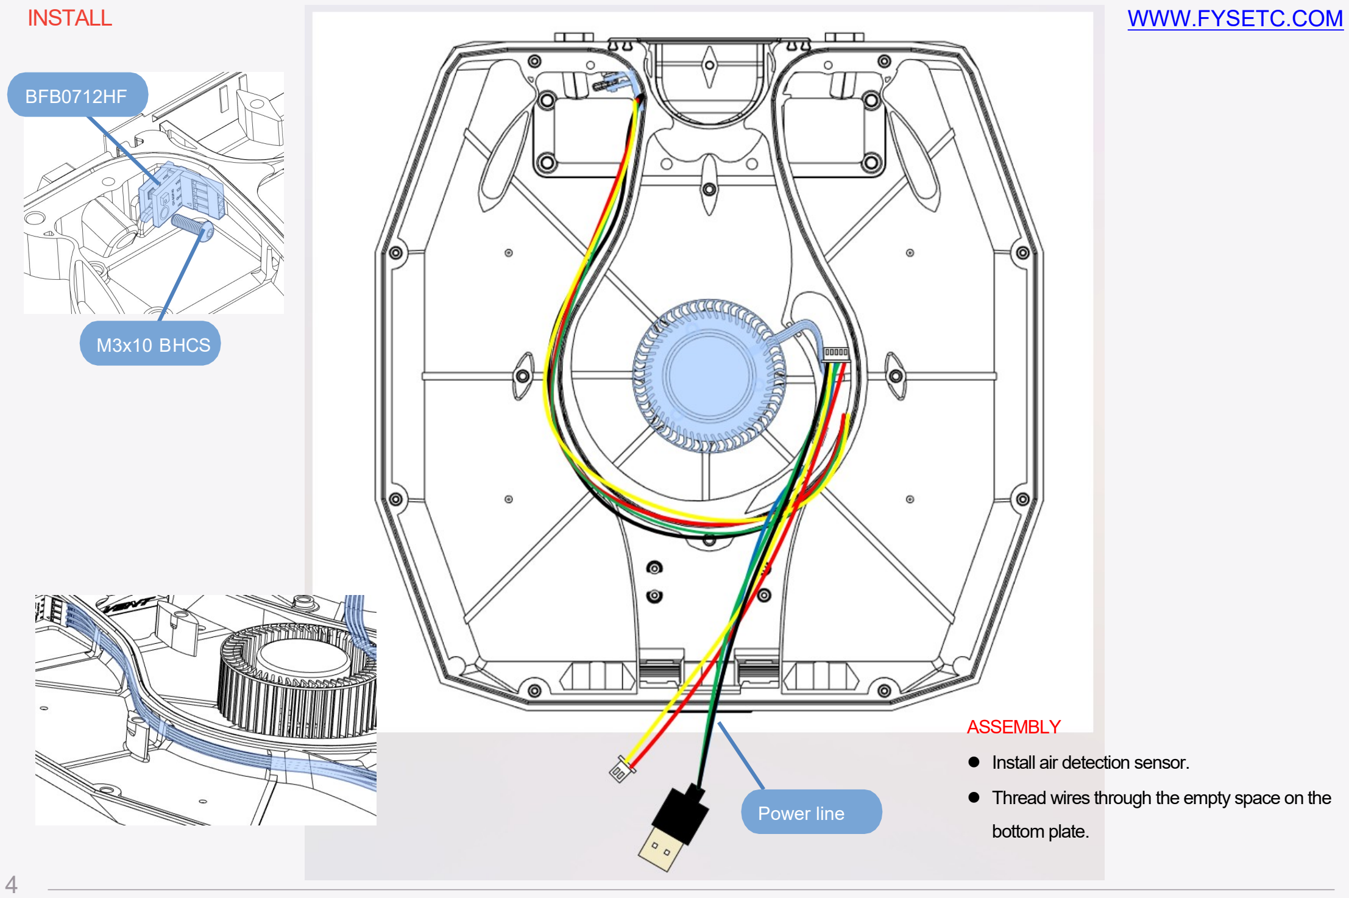
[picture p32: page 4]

INSTALL | WWW.FYSETC.COM

4

BFB0712HF

M3x10 BHCS

Power line

ASSEMBLY
l Install air detection sensor.
l Thread wires through the empty space on the bottom plate.

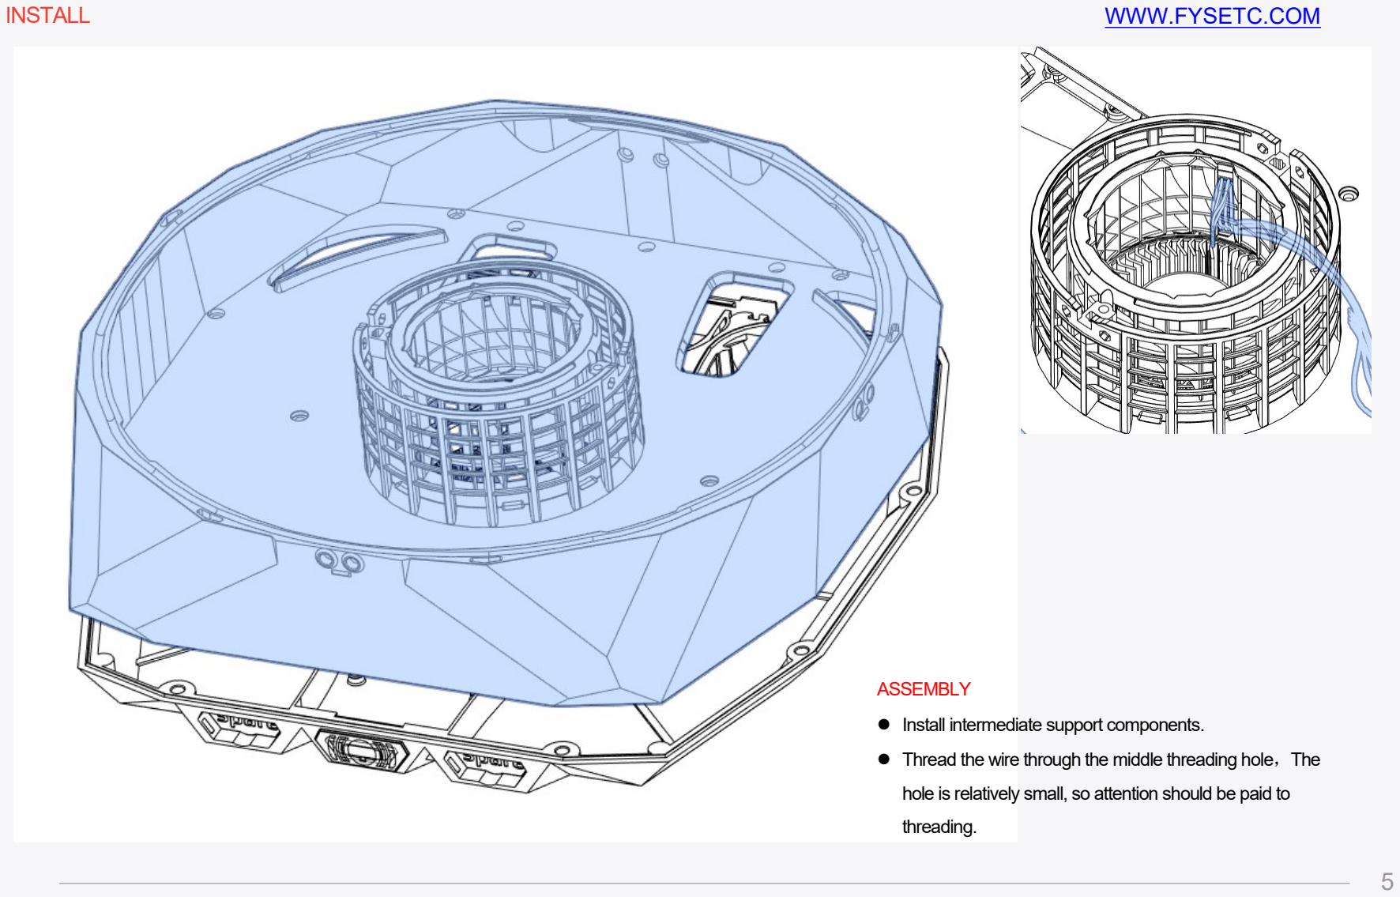
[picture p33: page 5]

### WWW.FYSETC.COM

5

### INSTALL

ASSEMBLY
l Install intermediate support components.
l Thread the wire through the middle threading hole，The hole is relatively small, so attention should be paid to threading.

### WWW.FYSETC.COM

6

M3x6 BHCS

### INSTALL

ASSEMBLY
l Use screws for locking.

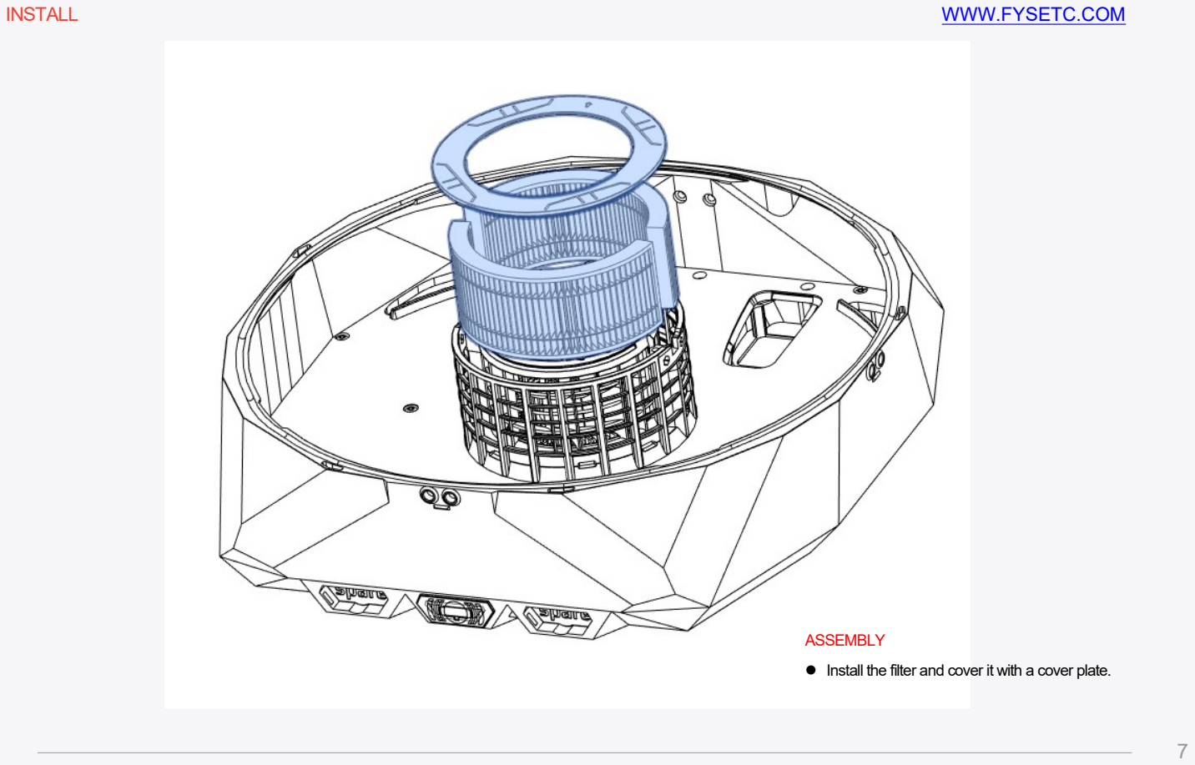
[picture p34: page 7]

### WWW.FYSETC.COM

7

### INSTALL

ASSEMBLY
l Install the filter and cover it with a cover plate.

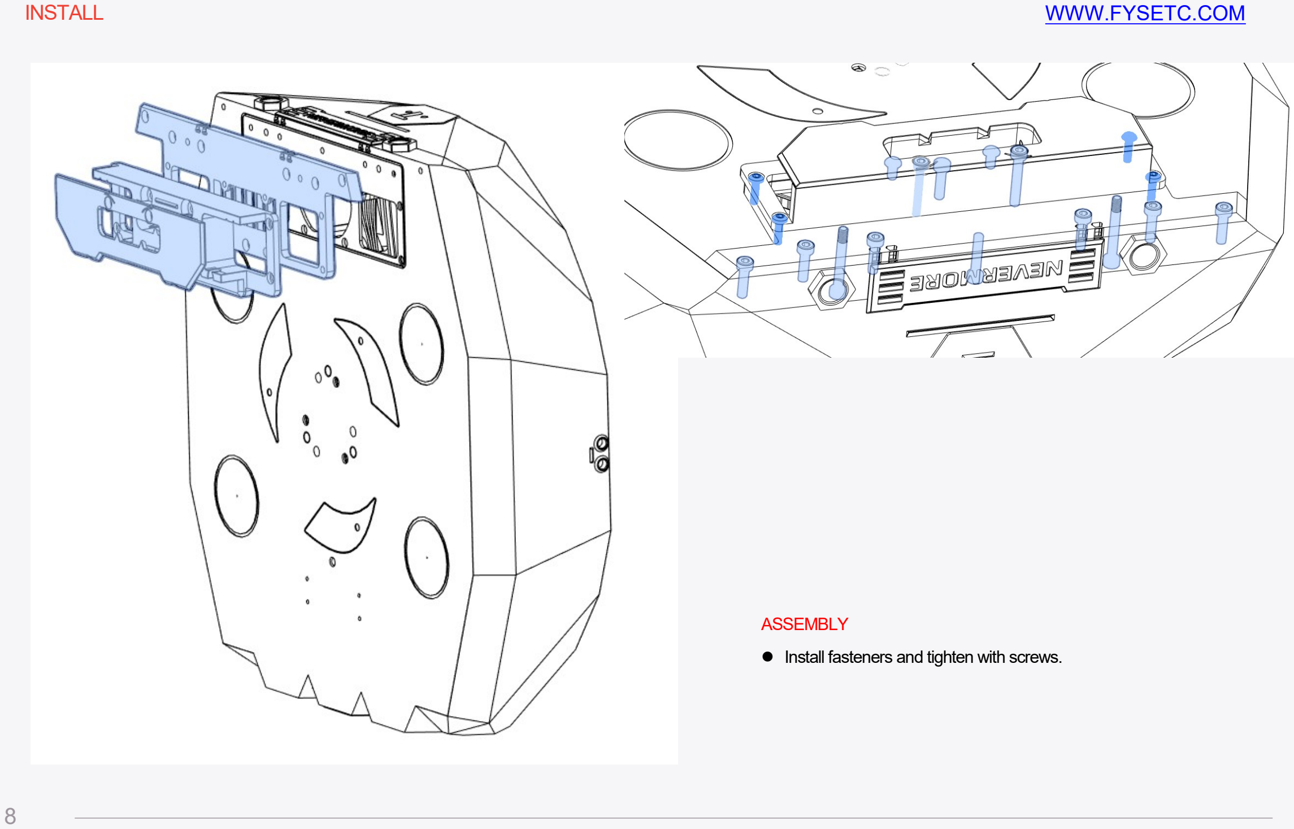
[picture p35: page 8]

### WWW.FYSETC.COM

8

### INSTALL

ASSEMBLY
l Install fasteners and tighten with screws.

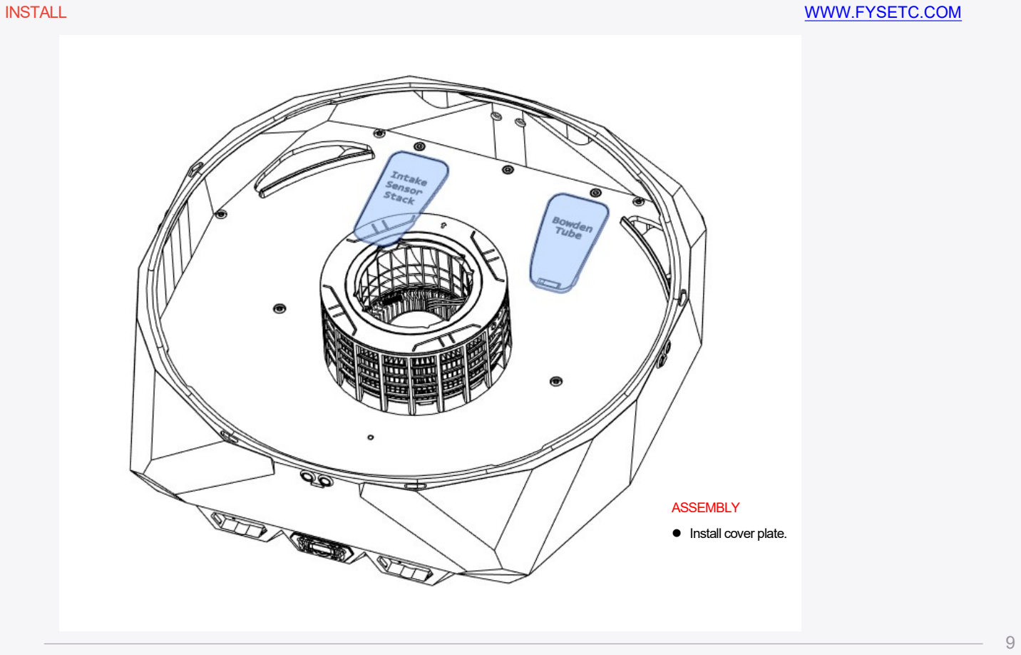
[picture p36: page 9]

### WWW.FYSETC.COM

9

### INSTALL

ASSEMBLY
l Install cover plate.

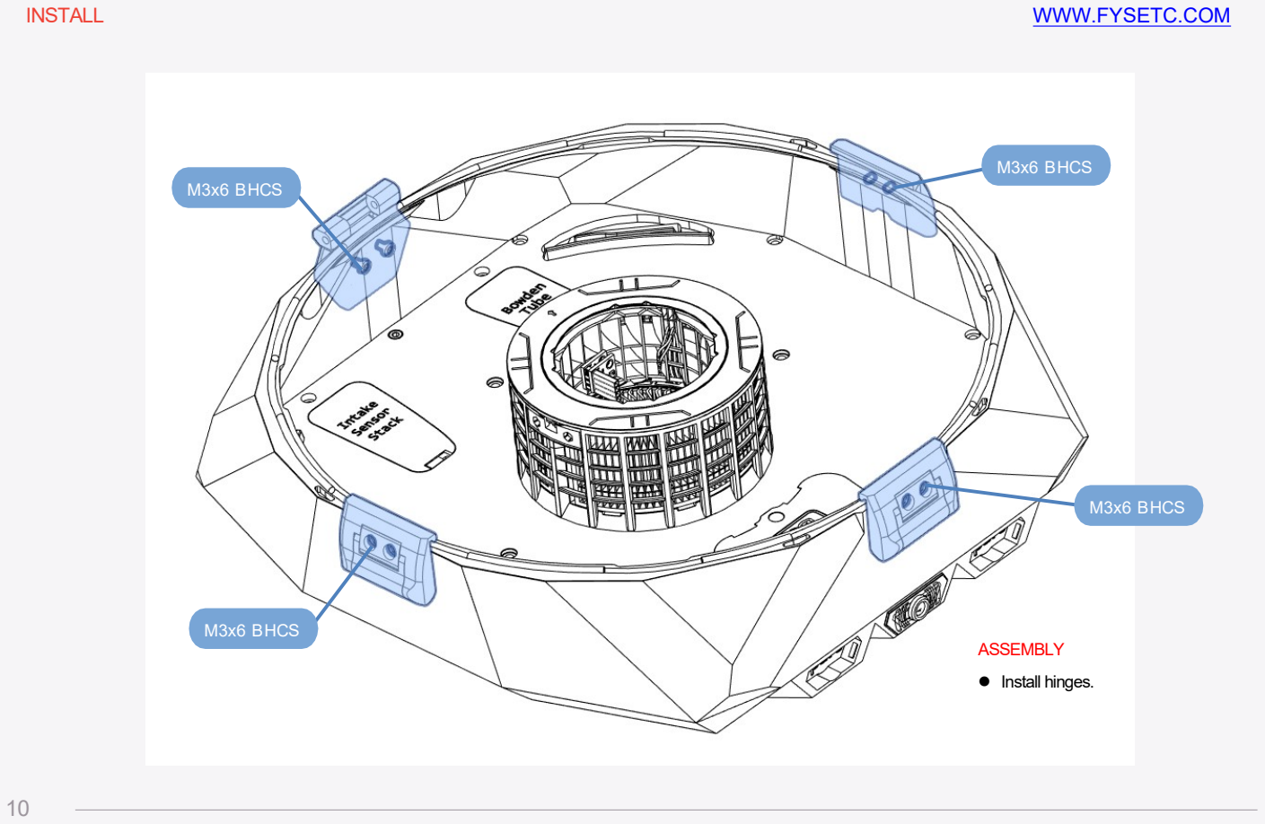
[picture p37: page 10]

INSTALL | WWW.FYSETC.COM

ASSEMBLY
l Install hinges.

M3x6 BHCS

M3x6 BHCS

M3x6 BHCS

M3x6 BHCS

10

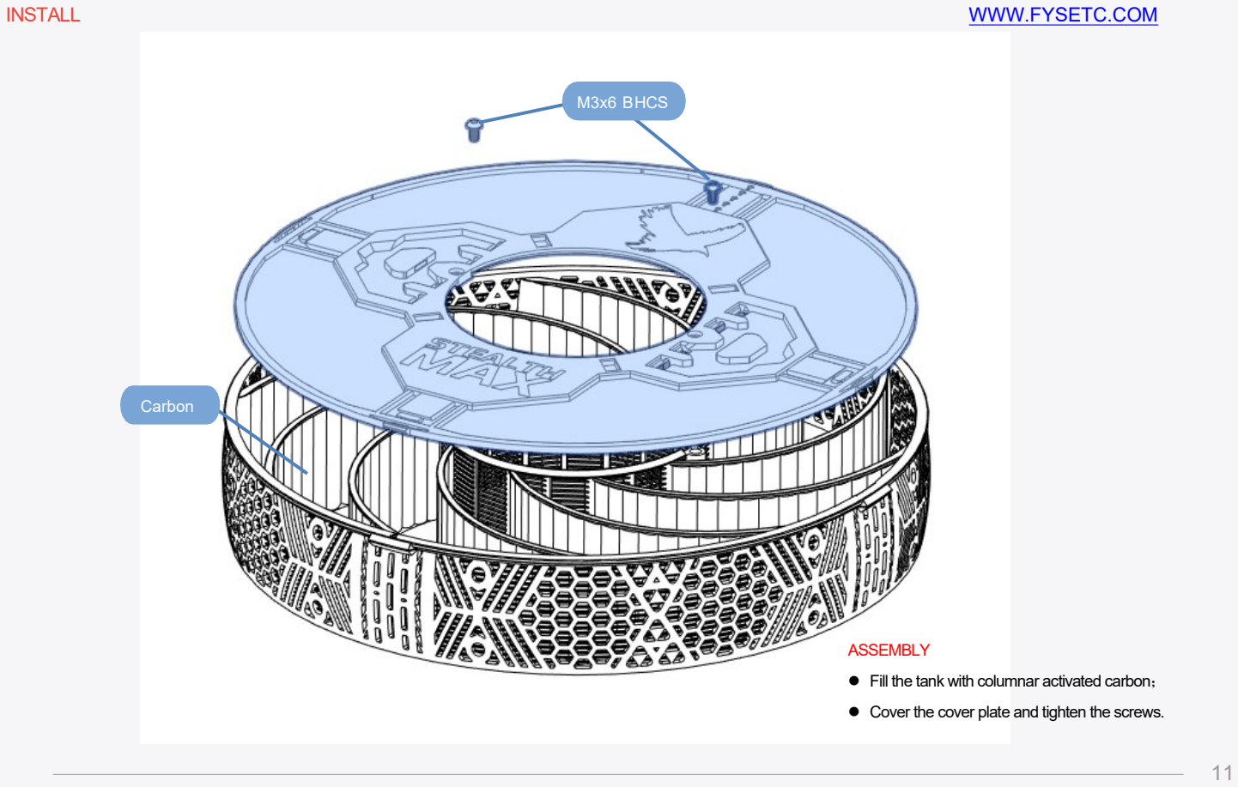
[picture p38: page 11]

### WWW.FYSETC.COM

11

### INSTALL

ASSEMBLY
l Fill the tank with columnar activated carbon； l Cover the cover plate and tighten the screws.

Carbon

M3x6 BHCS

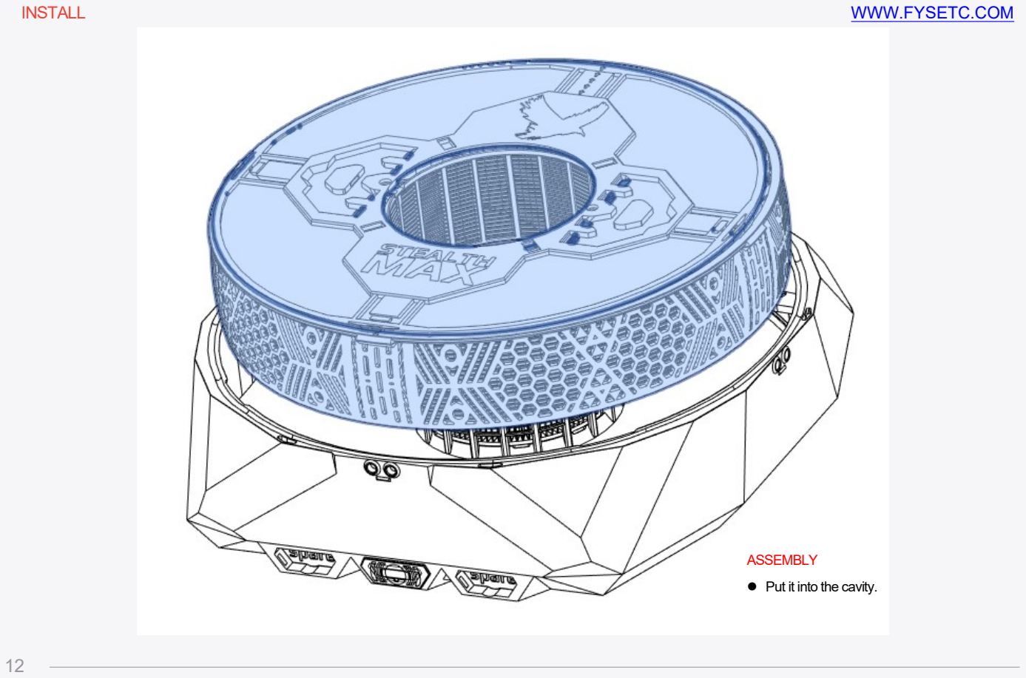
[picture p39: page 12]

### WWW.FYSETC.COM

12

### INSTALL

ASSEMBLY
l Put it into the cavity.

### WWW.FYSETC.COM

13

### INSTALL

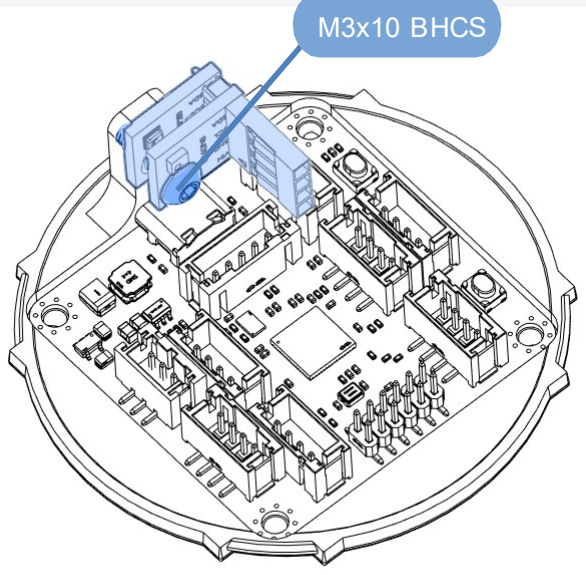
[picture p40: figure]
M3x10 BHCS

ASSEMBLY
l Install display screen，display screen USB port facing towards the print step.
l Install another sensor.

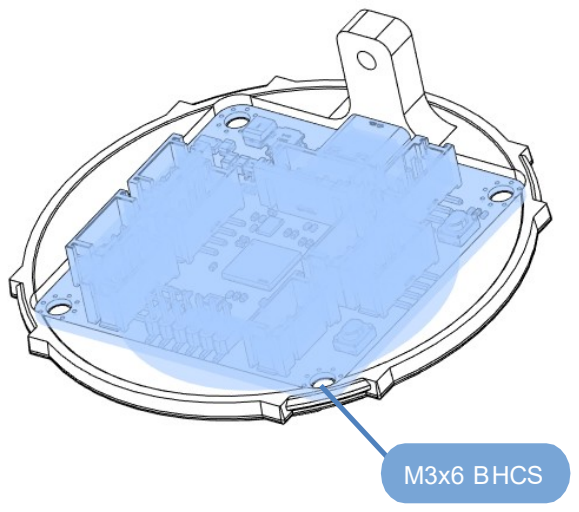
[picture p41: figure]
M3x6 BHCS
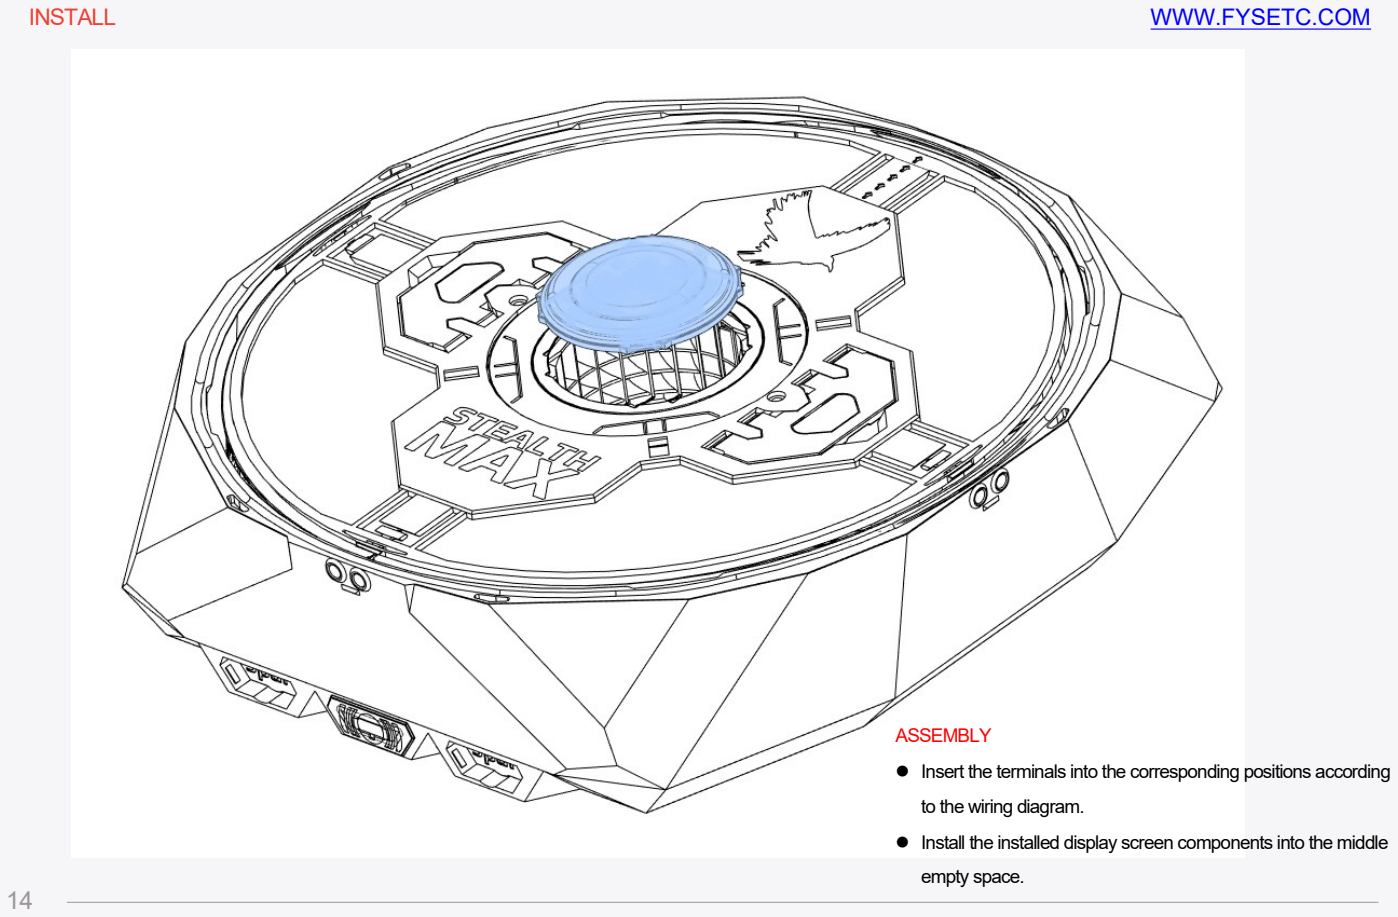
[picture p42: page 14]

### WWW.FYSETC.COM

14

ASSEMBLY
l Insert the terminals into the corresponding positions according to the wiring diagram.
l Install the installed display screen components into the middle empty space.

### INSTALL

### WWW.FYSETC.COM

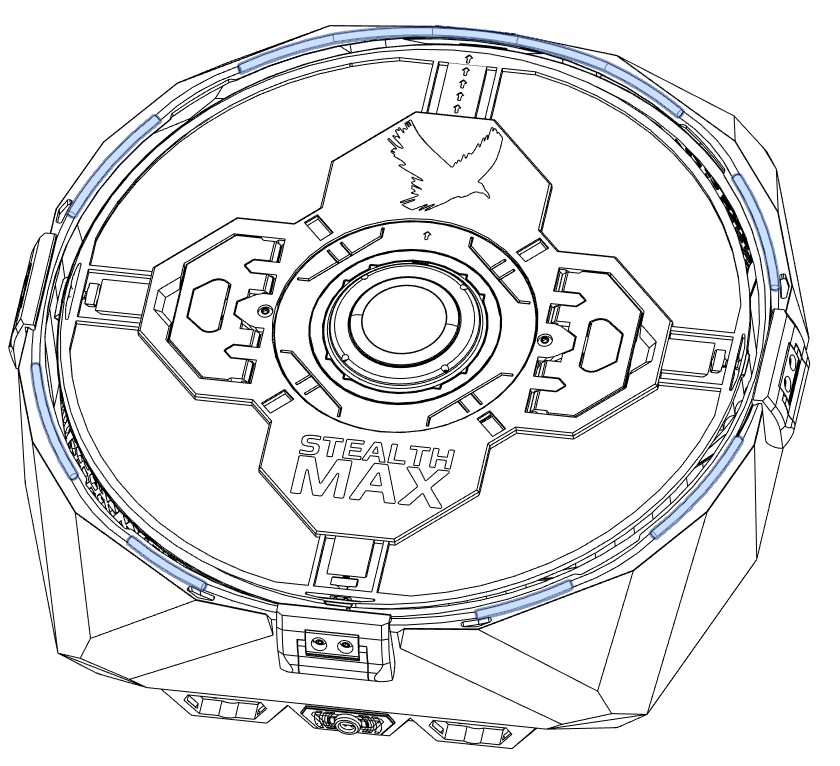
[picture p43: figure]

ASSEMBLY
l Install black sealing ring.

### INSTALL

15

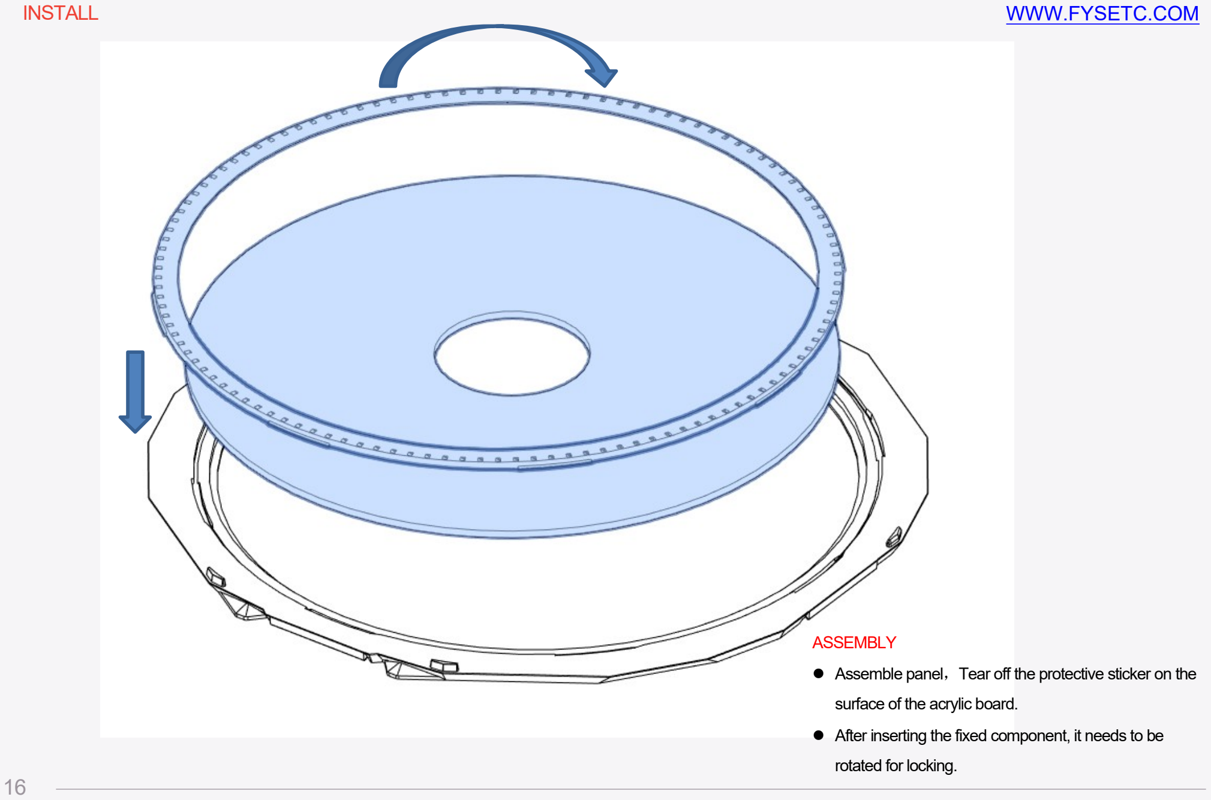
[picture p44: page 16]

### WWW.FYSETC.COM

ASSEMBLY
l Assemble panel，Tear off the protective sticker on the surface of the acrylic board.
l After inserting the fixed component, it needs to be rotated for locking.

### INSTALL

16

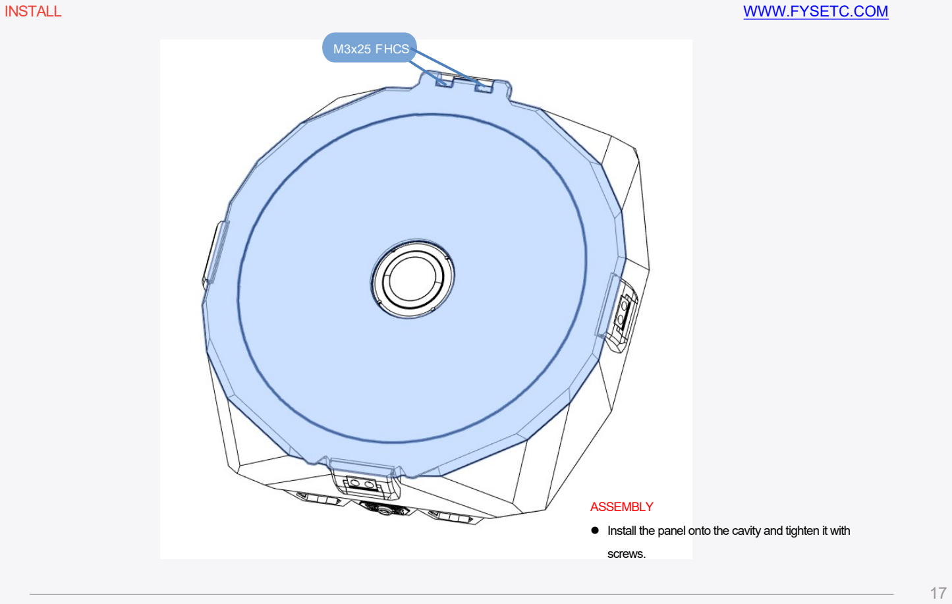
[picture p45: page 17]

### WWW.FYSETC.COM

ASSEMBLY
l Install the panel onto the cavity and tighten it with screws.

### INSTALL

M3x25 FHCS

17

### WWW.FYSETC.COM

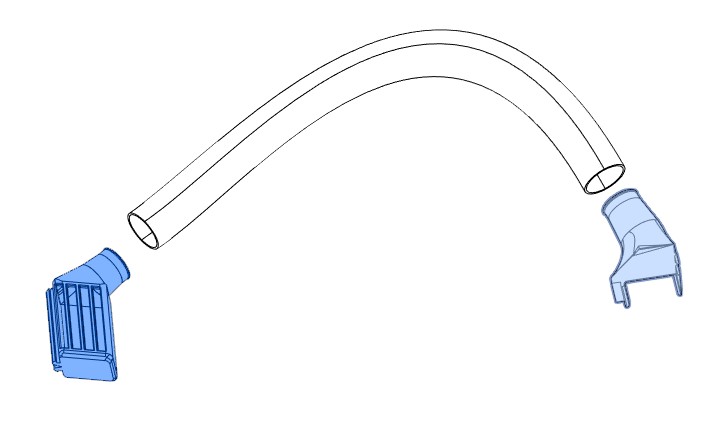
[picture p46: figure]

ASSEMBLY
l Install ventilation duct.

### INSTALL

18

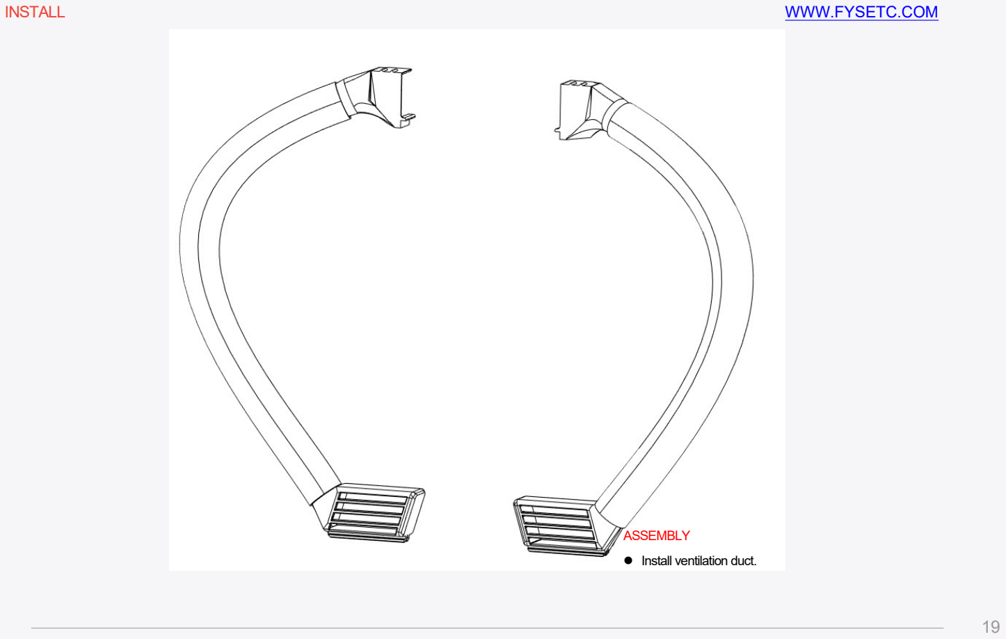
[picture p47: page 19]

### WWW.FYSETC.COM

ASSEMBLY
l Install ventilation duct.

### INSTALL

19

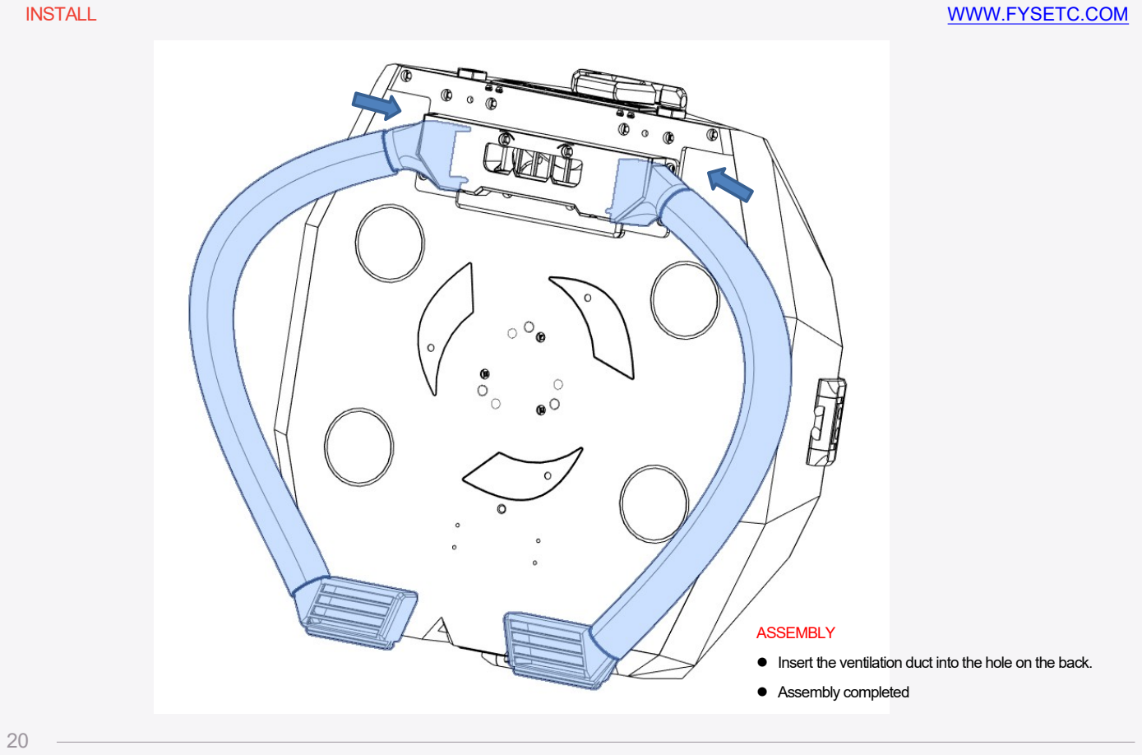
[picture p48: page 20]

### WWW.FYSETC.COM

ASSEMBLY
l Insert the ventilation duct into the hole on the back. l Assembly completed

### INSTALL

20

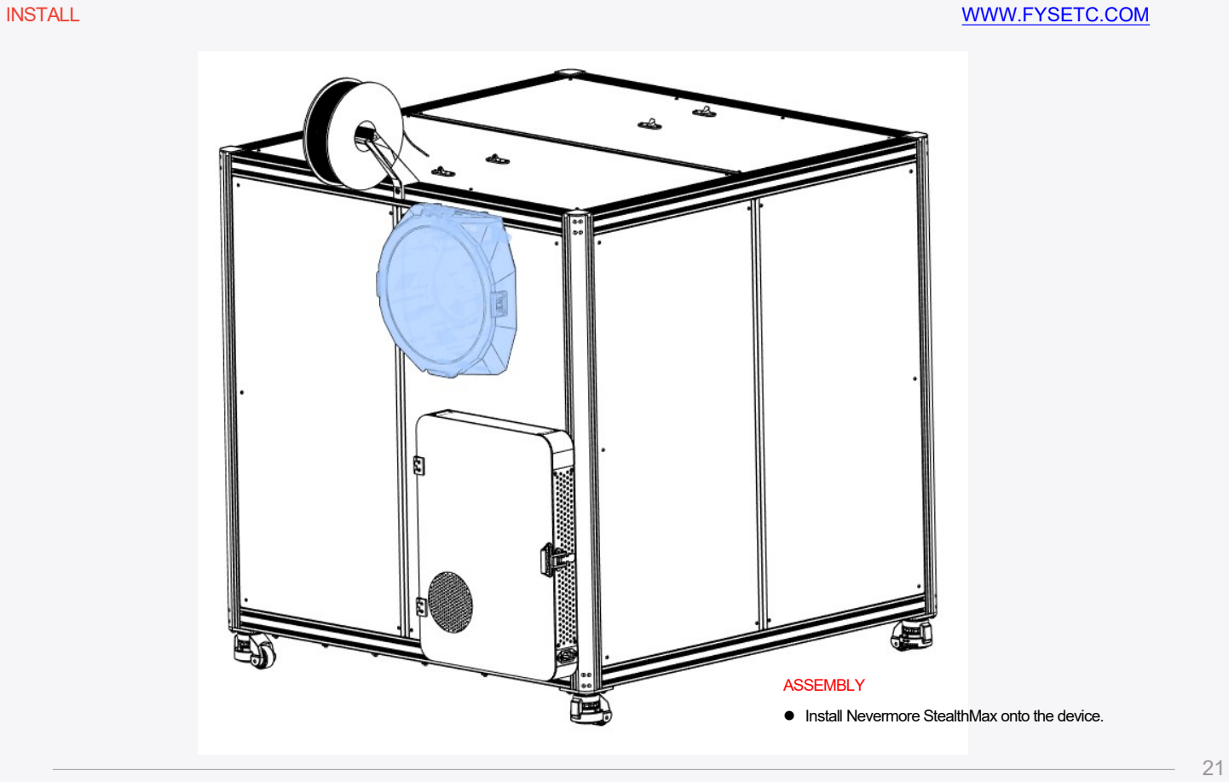
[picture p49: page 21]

INSTALL | WWW.FYSETC.COM

ASSEMBLY
l Install Nevermore StealthMax onto the device.

21

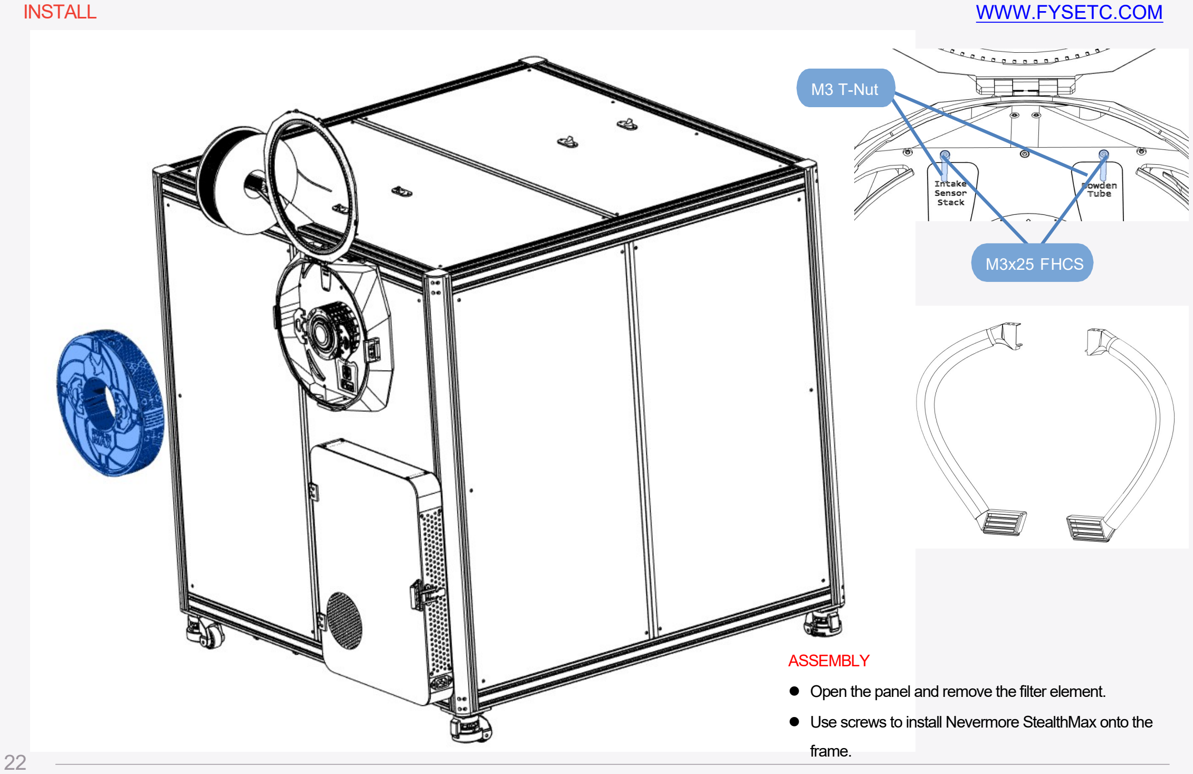
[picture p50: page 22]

INSTALL | WWW.FYSETC.COM

ASSEMBLY
l Open the panel and remove the filter element.
l Use screws to install Nevermore StealthMax onto the frame.

M3x25 FHCS

M3 T-Nut

22

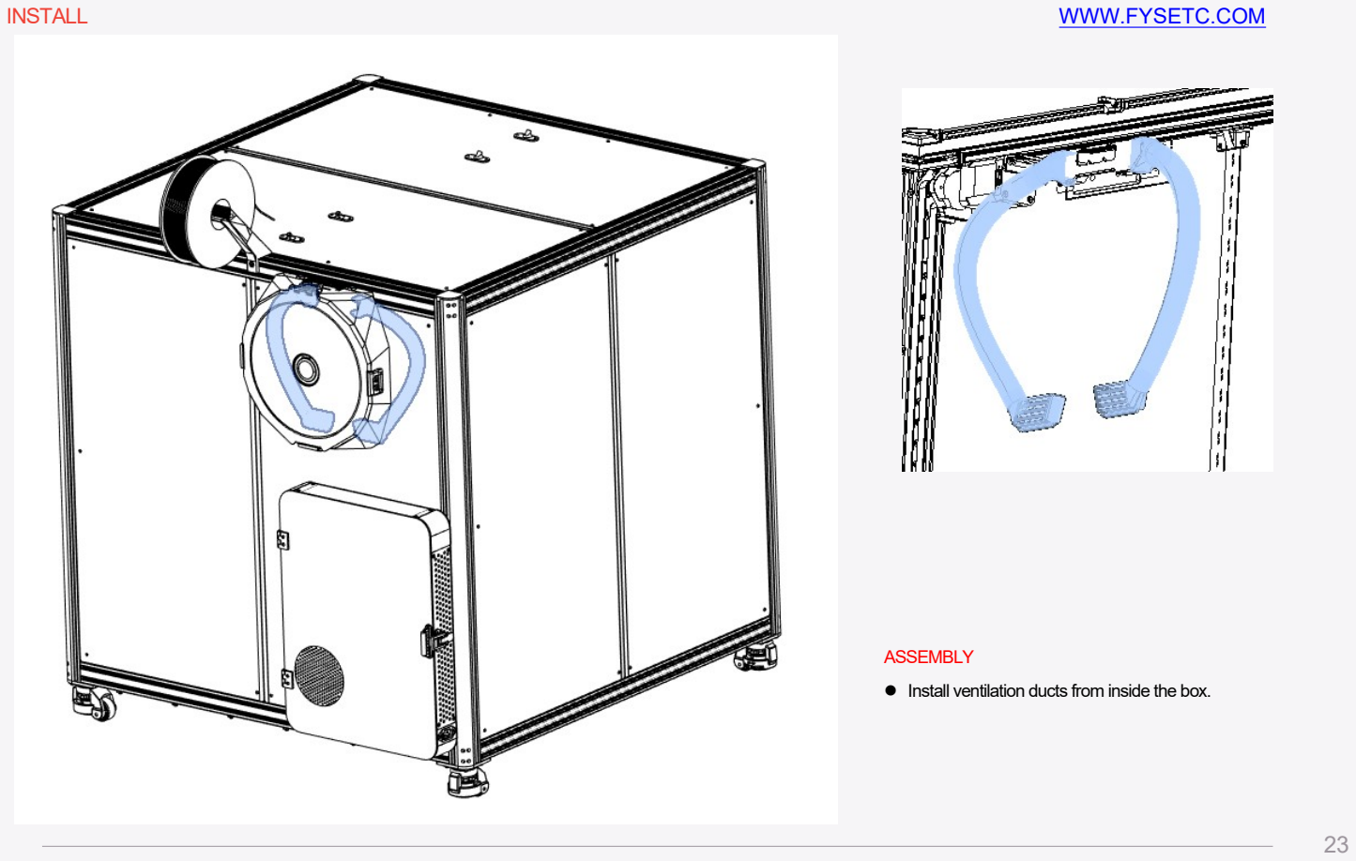
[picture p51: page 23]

INSTALL | WWW.FYSETC.COM

ASSEMBLY
l Install ventilation ducts from inside the box.

23

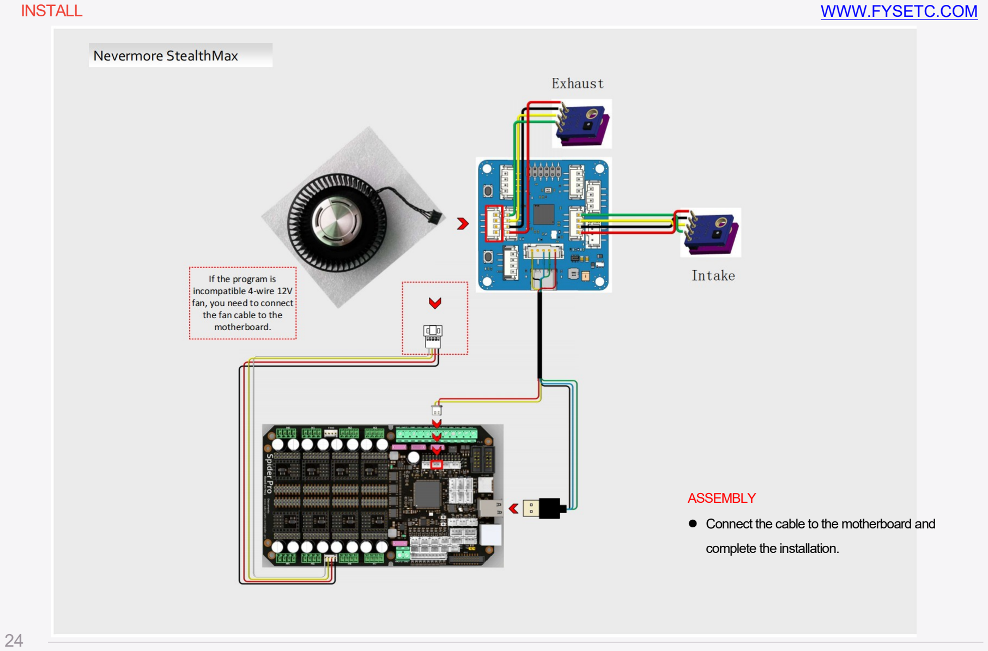
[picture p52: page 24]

INSTALL | WWW.FYSETC.COM

ASSEMBLY
l Connect the cable to the motherboard and complete the installation.

24

Enjoy your printer.

### WWW.FYSETC.COM

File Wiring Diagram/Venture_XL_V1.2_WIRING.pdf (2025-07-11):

E

Stealthburner CAN PCB

USB2

USE FYSETC TMC 2209 V3.1

# Spider Pro Venture XL

E

X Endstop

Nozzle Heating 5A MAX WSD3050

Temperature Sensor NTC/PT100/Thermocouple(Need AD597 add on)

3.3V 4.7K(0.1%)Pull Up

Z2

Rear-Right

Z3

Front-Right
Z0

Front-Left

Controller Fan

9015 FAN 24V

Y Endstop

Please make sure that your heating bed is in line with the voltage of your country or region. The high voltage version will hat very slowly when used at low voltage and may not reach the target temperature. The low-voltage version is used in the high-voltage version to heat up quickly, even exceeding the temperature you set, which is very dangerous.

## HOT SURFACE DO NOT TOUCH

### AC Heating Bed 110/220V INPUT

before powering up. 48V

Z1

Rear-Left

Hotend Fan 3007 FAN 24V

Hot bed 3 | Hot bed 2
Hot bed 4 | Hot bed 1

1 2 3 4

before powering up. 24V

Gantry light bar

Light bar power
board

Material break
detection

Decorative light
strips

A/B Motor Cooling FAn
4010 FAN 24V A/B Motor Cooling FAn

4010 FAN 24V

Four-way 25A SSR | V⁻MOTOR⁽24V⁾ GND A²A¹B1B2VIO⁽³.3V⁾ GND ENABLE (not used⁾MS1 (not used⁾MS2TX (not used⁾RX (not used⁾CLK STEP DIR DIAG | PDN

PDN: It is connected to TX for communication between TMC and MCU, using single wire. The

jumper cap shown in the figure must be setted before the drive module install. DIAG: It is used to go home without sensing, while ensuring that the jumper corresponding to the limit is in the closed state. ¹x Jumper cap

Print Cooling
Fan
5015 FAN 24V Hotend Fan 4010 FAN 24V

Led RGBW

Stealthburner CAN PCB

# Terminal docking 7x Jumper cap

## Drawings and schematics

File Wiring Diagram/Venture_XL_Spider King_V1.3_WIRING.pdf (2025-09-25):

# Spider King Venture XL V1.3

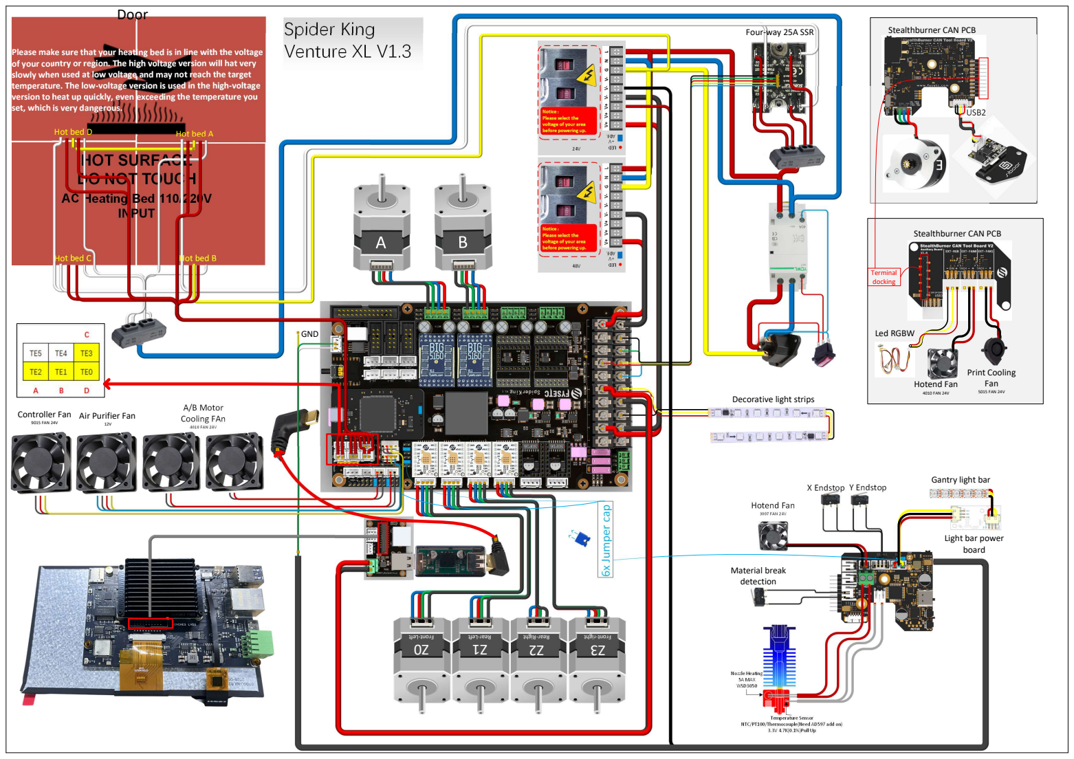
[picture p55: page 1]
X Endstop; 3.3V 4.7K(0.1%)Pull Up; Y Endstop; INPUT; Hot bed C; Hot bed B; Material break detection; 4010 FAN 24V; Print Cooling Fan; Led RGBW; Terminal; Controller Fan; 9015 FAN 24V; Air Purifier Fan; GND

Door

Stealthburner CAN PCB

Four-way 25A SSR

Please make sure that your heating bed is in line with the voltage of your country or region. The high voltage version will hat very slowly when used at low voltage and may not reach the target temperature. The low-voltage version is used in the high-voltage version to heat up quickly, even exceeding the temperature you set, which is very dangerous. Hot bed D | Hot bed A

USB2 USE FYSETC TMC 2209 V3.1

before powering up. 24V

HOT SURFACE
DO NOT TOUCH
AC Heating Bed 110/220V

before powering up. 48V

docking 6x Jumper cap

5015 FAN 24V Hotend Fan 4010 FAN 24V

Decorative light strips A/B Motor
Cooling FAn

Gantry light bar

Hotend Fan 3007 FAN 24V

Light bar power
board

Nozzle Heating 5A MAX WSD3050

Temperature Sensor NTC/PT100/Thermocouple(Need AD597 add on)

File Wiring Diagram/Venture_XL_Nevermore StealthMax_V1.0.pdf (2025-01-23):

## Nevermore StealthMax

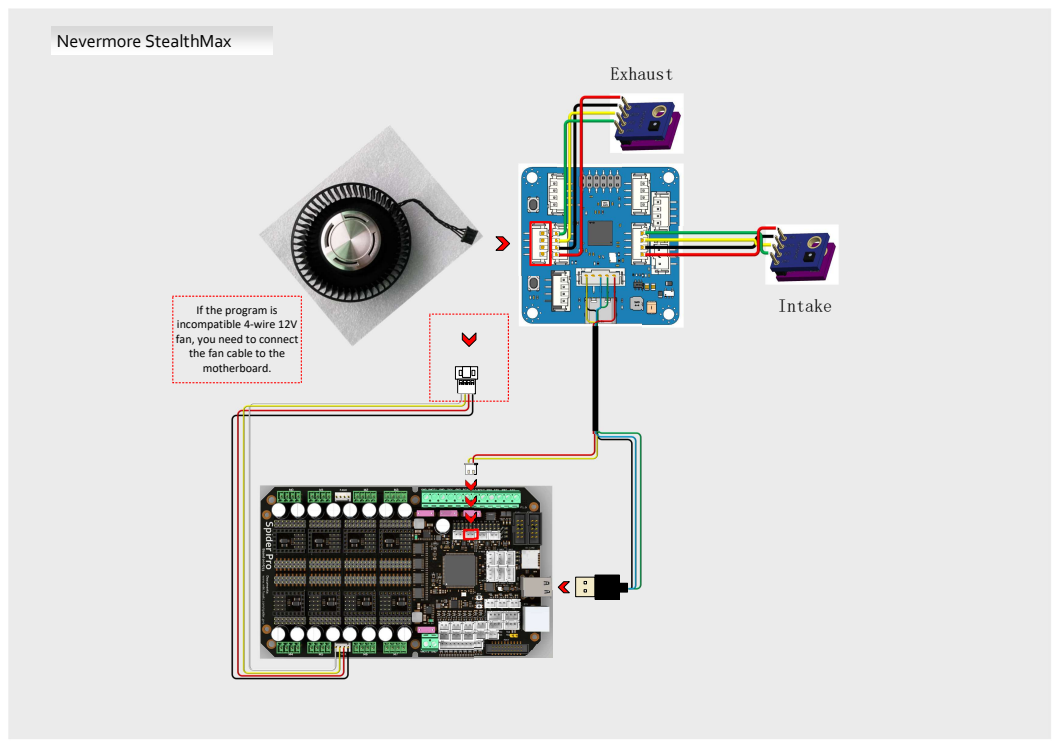
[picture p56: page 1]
Intake; Exhaust

If the program is
incompatible 4-wire 12V
fan, you need to connect
the fan cable to the
motherboard.

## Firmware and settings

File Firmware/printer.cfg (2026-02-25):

[include timelapse.cfg]
[include mainsail.cfg]
[include reshelper.cfg]
#[include testspeed.cfg]
[include KAMP_Settings.cfg]
[include stepper_spp.cfg]
[include Area_Bed.cfg]
# [include stealthburner_led_effects_barf.cfg]
# If you experience frequent "timer too close" errors, you can comment out the LED lighting effects to disable the RGB effects.
[exclude_object]
#[include Stealth_Max.cfg]


[printer]
kinematics: corexy           
max_velocity: 500      # 700 max tested      
max_accel: 40000       # 40000 max tested     
minimum_cruise_ratio: 0.5
max_z_velocity: 5           
max_z_accel: 50             
square_corner_velocity: 5.0  

[scanner]
# For more detailed configuration, please refer to: https://docs.cartographer3d.com/
# serial: /dev/serial/by-id/***
canbus_uuid: 489276ba49b7
canbus_interface: can2
backlash_comp: 0.03744
#   Backlash compensation distance for removing Z backlash before measuring
#   the sensor response.
# 
#   Offsets are measured from the centre of your coil, to the tip of your nozzle 
#   on a level axis. It is vital that this is accurate. 
x_offset: 0                          
#adjust for your offset
y_offset: 23                       
#adjust for your offset
calibration_method: scan
sensor: cartographer
sensor_alt: carto
#alternate name to call commands. CARTO_TOUCH etc
mesh_runs: 2
#Number of passes to make during mesh scan.
#scanner_touch_z_offset: 0.05         
#this is the default and will be overwritten and added to the DO NOT SAVE area by using UI to save z offset

[mcu]
# For more information about Spider Pro, please refer to: https://github.com/FYSETC/Spider_Pro
# serial: /dev/serial/by-path/platform-fd840000.usb-usb-0:1:1.0
# serial: /dev/serial/by-id/***                      
canbus_uuid: 682f8c06d5f6
#canbus_uuid: 0bbd682510f3
canbus_interface: can2
# serial: ttyS10
# baud: 250000

[mcu sb_combo]
# For more information about SB Combo, please refer to: https://wiki.fysetc.com/SB_Combo_V2/  &  https://github.com/FYSETC/SB_Combo_V2
# serial: /dev/serial/by-id/***
canbus_uuid: 8d115dc1ca43
canbus_interface: can2
# make flash FLASH_DEVICE=0483:df11
# Follow the instruction here https://www.klipper3d.org/CANBUS.html to get CAN id

##  In MOTOR Connector
[extruder]
step_pin: sb_combo:PB3 #PA7
dir_pin: !sb_combo:PA8 #PA5
enable_pin: !sb_combo:PA15 #PB4 

##  Update value below when you perform extruder calibration
##  If you ask for 100mm of filament, but in reality it is 98mm:
##  rotation_distance = <previous_rotation_distance> * <actual_extrude_distance> / 100
##  22.6789511 is a good starting point for Bondtech 5mm gears
##  34.37086 for Bondtech 8mm gears (Galileo)
rotation_distance: 4.45   #22.6789511   #Bondtech 5mm Drive Gears
##  Update Gear Ratio depending on your Extruder Type
##  Use 50:17 for Afterburner/Clockwork (BMG Gear Ratio)
##  Use 80:20 for M4, M3.1
##  Use 7.5:1 for Galileo
##  gear_ratio: 50:10               #for Stealthburner/Clockwork2 BMG Gear Ratio
microsteps: 16
full_steps_per_rotation: 200    #200 for 1.8 degree, 400 for 0.9 degree
nozzle_diameter: 0.400
filament_diameter: 1.75
heater_pin: sb_combo:PC15 #PA8 # Heat
## Check what thermistor type you have. See https://www.klipper3d.org/Config_Reference.html#common-thermistors for common thermistor types.
## Use "Generic 3950" for NTC 100k 3950 thermistors
sensor_type: Generic 3950
sensor_pin: sb_combo:PA6 #PA0 # TH
min_temp: -273.15 #1 #-273.15 # 1 #zzcatvs mod
max_temp: 99999 #360 #99999 # 360 #zzcatvs mod
max_power: 1.0
min_extrude_temp: 10
#control = pid
#pid_kp = 26.213
#pid_ki = 1.304
#pid_kd = 131.721
##  Try to keep pressure_advance below 1.0
#pressure_advance: 0.02 #0.05
##  Default is 0.040, leave stock
#pressure_advance_smooth_time: 0.040
pressure_advance: 0.025       
pressure_advance_smooth_time: 0.035    
max_extrude_cross_section: 5000.0
max_extrude_only_distance: 500.0


[tmc2209 extruder]
uart_pin: sb_combo:PA10
tx_pin: sb_combo:PA9
interpolate: false
run_current: 0.7
sense_resistor: 0.110
stealthchop_threshold: 0
##diag_pin: sb_combo:PB5

[adxl345]
cs_pin: sb_combo:PB12
spi_software_sclk_pin: sb_combo:PB13
spi_software_mosi_pin: sb_combo:PB15
spi_software_miso_pin: sb_combo:PB14
axes_map: z,-y,-x

[resonance_tester]
accel_chip: adxl345
probe_points:
    300,300,30 # an example

[input_shaper]
#shaper_type_x = zv
#shaper_freq_x = 39
#shaper_type_y = mzv
#shaper_freq_y = 32.6

#####################################################################
# RGB
#####################################################################

# 5V RGB LOGO light board located on Stealthburner, 8 RGB + 2 RGBW.    
[neopixel sb_leds]
pin: sb_combo: PC14  #EXT-RGB=PB11 #RGB=PB11
chain_count: 10
color_order: GRB,GRB,GRB,GRB,GRB,GRB,GRB,GRB,RGBW,RGBW
initial_RED: 0.5 #0.5
initial_GREEN: 0.5
initial_BLUE: 0.5 #0.5
initial_WHITE: 0.5 #0.5

# 5V RGB light strip horizontally on the X axis，55 RGB.
[neopixel print_light]
pin: sb_combo: PA0  #IO.2=PA0
chain_count: 55
color_order: GRB
initial_RED: 0.5 #0.5
initial_GREEN: 0.5
initial_BLUE: 0.5 #0.5
#initial_WHITE: 0.5 #0.5

# 24V RGB light strip Vertically on the Z axis，2 x 14 RGB units ( 6 per ).
[neopixel lamp_rgb]
pin: PA1  
chain_count: 28
color_order: BRG
initial_RED: 1.0 
initial_GREEN: 1.0
initial_BLUE: 1.0

#####################################################################
# FANS on SB Combo
#####################################################################

[fan]
pin: sb_combo:PB0    #EXT-FAN0 #FAN1=PB5

[heater_fan hotend_fan]
pin: sb_combo:PB7    #EXT-FAN1 #FAN0=PB6
shutdown_speed: 0

[temperature_fan SB_Driver]
##	Controller fan - FAN2 Connector
pin: sb_combo:PA4 #FAN2
max_power: 1.0
shutdown_speed: 0.0
kick_start_time: 0.5
sensor_type: NTC 100K MGB18-104F39050L32
sensor_pin: sb_combo:PB1 
control:watermark
min_temp: 0
max_temp: 150
target_temp: 40.0

#####################################################################
# FANS on Spider Pro
#####################################################################

# [temperature_fan Stepper_X]
# ##	Controller fan - FAN2 Connector
# pin: PA15 #FAN5
# max_power: 1.0
# shutdown_speed: 0.0
# kick_start_time: 0.5
# sensor_type: NTC 100K MGB18-104F39050L32
# sensor_pin: PC1
# control:watermark
# min_temp: 0
# max_temp: 150
# target_temp: 40.0

# [temperature_fan Stepper_Y]
# ##	Controller fan - FAN2 Connector
# pin: PD14 #FAN4
# max_power: 1.0
# shutdown_speed: 0.0
# kick_start_time: 0.5
# sensor_type: NTC 100K MGB18-104F39050L32
# sensor_pin: PC0
# control:watermark
# min_temp: 0
# max_temp: 150
# target_temp: 40.0

[controller_fan A_motor_fan]
pin:PA15
max_power:1.0
shutdown_speed:0
#cycle_time:
#hardware_pwm:
#kick_start_time:
#off_below:
#tachometer_pin:PD1
#tachometer_ppr:
#tachometer_poll_interval:
#enable_pin:PE8
#fan_speed: 1.0
#idle_timeout:
idle_speed:0.3
#heater:
stepper: stepper_x


[controller_fan B_motor_fan]
pin:PD14
max_power:1.0
shutdown_speed:0
#cycle_time:
#hardware_pwm:
#kick_start_time:
#off_below:
#tachometer_pin:PD1
#tachometer_ppr:
#tachometer_poll_interval:
#enable_pin:PE8
#fan_speed: 1.0
#idle_timeout:
idle_speed:0.3
#heater:
stepper: stepper_y

[fan_generic StealMax_fan]
pin:PC8
max_power:1.0
#shutdown_speed:
#cycle_time:
#hardware_pwm:
#kick_start_time:
off_below:0.1
tachometer_pin:PB7
#tachometer_ppr:
#tachometer_poll_interval:
#enable_pin:
#   See the "fan" section for a description of the above parameters.

[controller_fan board_driver_fan]
pin:PB9
max_power:1.0
shutdown_speed:0
#cycle_time:
#hardware_pwm:
#kick_start_time:
#off_below:
tachometer_pin:PB1
#tachometer_ppr:
#tachometer_poll_interval:
#enable_pin:PC8
#   See the "fan" section for a description of the above parameters.
#fan_speed: 1.0
#   The fan speed (expressed as a value from 0.0 to 1.0) that the fan
#   will be set to when a heater or stepper driver is active.
#   The default is 1.0
#idle_timeout:
#   The amount of time (in seconds) after a stepper driver or heater
#   was active and the fan should be kept running. The default
#   is 30 seconds.
idle_speed:0.3
#   The fan speed (expressed as a value from 0.0 to 1.0) that the fan
#   will be set to when a heater or stepper driver was active and
#   before the idle_timeout is reached. The default is fan_speed.
#heater:
stepper: stepper_z
#   Name of the config section defining the heater/stepper that this fan
#   is associated with. If a comma separated list of heater/stepper names
#   is provided here, then the fan will be enabled when any of the given
#   heaters/steppers are enabled. The default heater is "extruder", the
#   default stepper is all of them.

#####################################################################
#      X/Y Stepper Settings
#####################################################################

[stepper_x]

position_endstop: 657.5
position_max: 657.5
homing_speed: 200 
homing_retract_dist: 0
homing_positive_dir: true
endstop_pin:sb_combo:PA2

[stepper_y]
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

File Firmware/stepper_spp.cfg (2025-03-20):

####################################################################
#      X/Y Stepper Settings
#####################################################################

# By default, Klipper places the TMC drivers in "spreadCycle" mode. 
# If the driver supports "stealthChop" then it can be enabled by 
# adding stealthchop_threshold: 999999 to the TMC config section.

[stepper_y]
##  Connected to M6 (A Motor)
step_pin: PG13
dir_pin: !PG8
enable_pin: !PG9
microsteps: 16
rotation_distance: 40
full_steps_per_rotation: 200

[tmc5160 stepper_y]
# spi_speed:
# spi_bus:spi5
spi_software_mosi_pin: PF9
spi_software_miso_pin: PF8
spi_software_sclk_pin: PF7
cs_pin: PG3
interpolate: true   #False 
run_current: 2.0
hold_current: 0.5
stealthchop_threshold: 0
sense_resistor: 0.075
#diag0_pin:PF2
#driver_SGT: 1

[stepper_x]
##  Connected to M7 (B Motor)
step_pin: PE1
dir_pin: !PE0
enable_pin: !PB2
rotation_distance: 40
microsteps: 16
full_steps_per_rotation:200  #set to 400 for 0.9 degree stepper

[tmc5160 stepper_x]
# spi_speed:
# spi_bus:spi5
spi_software_mosi_pin: PF9
spi_software_miso_pin: PF8
spi_software_sclk_pin: PF7
cs_pin: PD9
interpolate: true  #False 
run_current: 2.0
hold_current: 0.5
stealthchop_threshold: 0
sense_resistor: 0.075
#diag0_pin:PG11
#driver_SGT: 1

# [stepper_x1]
# ##  Connected to M5 
# step_pin: PE3
# dir_pin: PE4
# enable_pin: !PE2
# microsteps: 16
# rotation_distance: 40
# full_steps_per_rotation: 200

# [tmc5160 stepper_x1]
# spi_speed:
# spi_bus:spi5
# spi_software_mosi_pin: PF9
# spi_software_miso_pin: PF8
# spi_software_sclk_pin: PF7
# cs_pin: PC15
# interpolate: False   #true   False 
# run_current: 0.8
# #hold_current: 0.5
# stealthchop_threshold: 0
# sense_resistor: 0.075
# diag0_pin:PG5
# #driver_SGT: 1

# [stepper_y1]
# ##  Connected to M4
# step_pin: PE5
# dir_pin: PC13
# enable_pin: !PE6
# rotation_distance: 40
# microsteps: 16
# full_steps_per_rotation:200

# [tmc5160 stepper_y1]
# spi_speed:
# spi_bus:spi5
# spi_software_mosi_pin: PF9
# spi_software_miso_pin: PF8
# spi_software_sclk_pin: PF7
# cs_pin: PC14
# interpolate: False
# run_current: 0.8
# #hold_current: 0.5
# stealthchop_threshold: 0
# sense_resistor: 0.075
# diag0_pin:PG0
# #driver_SGT: 1


#####################################################################
#   Z Stepper Settings
#####################################################################

## In M0 Position
## Z0 Stepper - Front Left
[stepper_z]
step_pin: PG7
dir_pin: PG6
enable_pin: !PE11
rotation_distance: 40
gear_ratio: 27:1
microsteps: 16

[tmc2209 stepper_z]
uart_pin: PD2
interpolate: false
run_current: 1.8
hold_current: 0.5
sense_resistor: 0.110
stealthchop_threshold: 0
#diag_pin:PG1

##  In M1 Position
##  Z1 Stepper - Rear Left
[stepper_z1]
step_pin: PD11
dir_pin: !PD10
enable_pin: !PG10
rotation_distance: 40
gear_ratio: 27:1
microsteps: 16

[tmc2209 stepper_z1]
uart_pin: PE15
interpolate: false
run_current: 1.8
hold_current: 0.5
sense_resistor: 0.110
stealthchop_threshold: 0
#diag_pin:PG2

##  In M2 Position
##  Z2 Stepper - Rear Right
[stepper_z2]
step_pin: PG14
dir_pin: PG12
enable_pin: !PG15
rotation_distance: 40
gear_ratio: 27:1
microsteps: 16

[tmc2209 stepper_z2]
uart_pin: PD8
interpolate: false
run_current: 1.8
hold_current: 0.5
sense_resistor: 0.110
stealthchop_threshold: 0
#diag_pin:PD3

##  In M3 Position
##  Z3 Stepper - Front Right
[stepper_z3]
step_pin: PD4
dir_pin: !PD6
enable_pin: !PD5
rotation_distance: 40
gear_ratio: 27:1
microsteps: 16

[tmc2209 stepper_z3]
uart_pin: PD7
interpolate: false
run_current: 1.8
hold_current: 0.5
sense_resistor: 0.110
stealthchop_threshold: 0
#diag_pin:PA0

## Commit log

2025-01-23 Data Update
    [7 inch display housing_1_x1.STL, 7 inch display housing_2_x1.STL, 7 inch display housing_3_x1.STL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]
2025-02-08 Update Files
    [Camera cable cover_x1.STL]
2025-02-21 Print updates
    [0a.1_BackPanelMount_BPM_1.STL, 1.3a_BowdenCap_Closed.stl, 1.3b_BowdenCap_Open.stl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]
2025-03-13 update config
    [Area_Bed.cfg, printer.cfg, stepper_spp.cfg]
2025-03-20 File Modification
    [[a]_xy_joint_cable_bridge_2hole.stl, [a]_xy_joint_cable_bridge_3hole.stl]
2025-03-21 Document Updates
    [SB_Dragon_Cutting_Printhead_Back.STL, SB_Dragon_Cutting_Printhead_Front.STL]
2025-04-17 Print file updates
    [Chain_Anchor_3_Hole_V2_Trident-G.stl, Chain_Anchor_3_Hole_V2_Trident.STL, Chain_Anchor_3_Hole_V2_Trident_x1.STL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]
2025-04-30 Create Motor line repair.jpg
2025-08-11 File Updates
    [Depressor.stl, Depressor_Mount.stl]
2025-09-08 Mainboard wiring diagram updated
2025-11-27 Limit switch update
    [Y limit bracket（Mushroom head）_X2.STL]
2026-02-25 Update printer.cfg
    Commented out Z_Tilt section
    [printer.cfg]
